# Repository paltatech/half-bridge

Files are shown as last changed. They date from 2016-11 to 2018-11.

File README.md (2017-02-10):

# TO247 Inverter power stage
This is the hardware repository of a 3 phase inverter, UNTESTED but designed with the following specs in mind:

* 70kw nominal, 150kw peak
* TO247 IGBT to allow for easy silicon upgrades and power capabilities. Its also cheaper.
* Watercooled
* Embedded security features (desaturation, soft turn off, reinforced isolation)


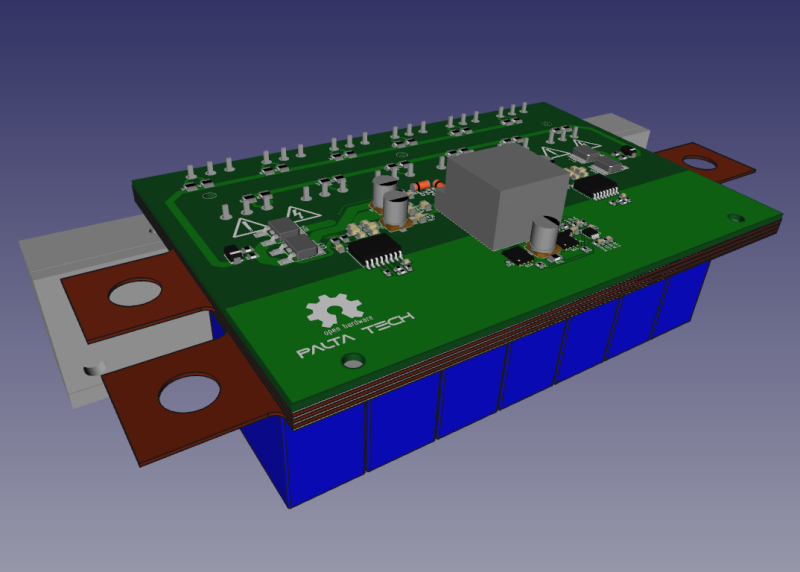
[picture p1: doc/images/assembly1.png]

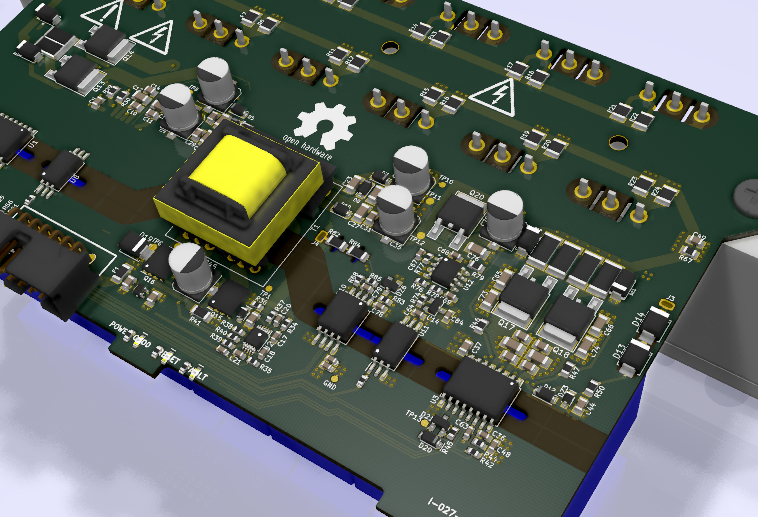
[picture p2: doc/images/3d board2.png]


You can also check the layout [here](https://eyrie.io/board?id=7261e811b9074e0fb00fe3fcbbaa14d9) 

Will need some cnc milling, components, a pcb, and some spot welding

Made open source with open source tools (kicad, freecad)

## Bill of materials
BOM, pcb gerbers, and custom parts can be found in [fabrication files](https://bitbucket.org/paltatech/half-bridge) directory

## License
This documentation describes Open Hardware and is licensed under the CERN OHL v. 1.2

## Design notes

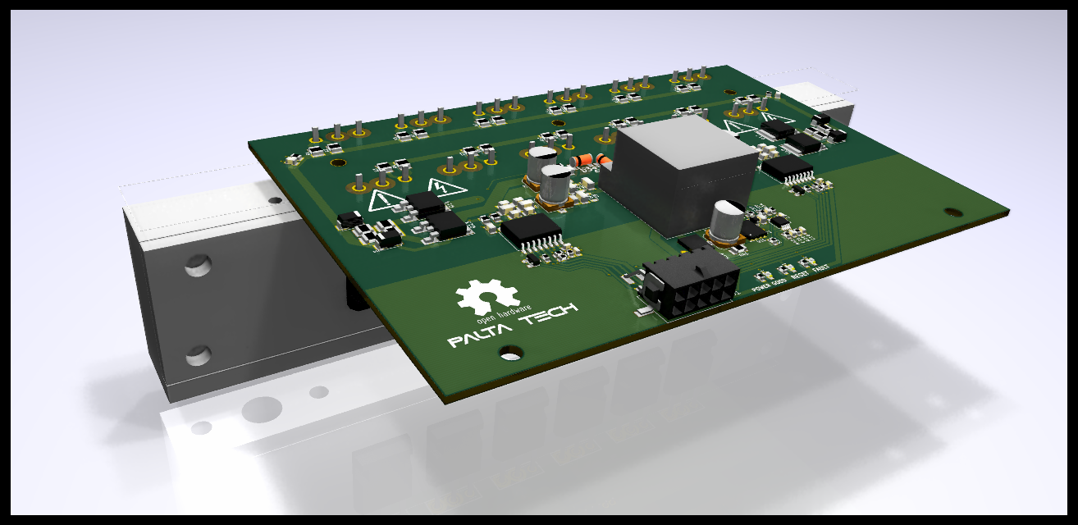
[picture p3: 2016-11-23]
doc/images/pcb_preview.png

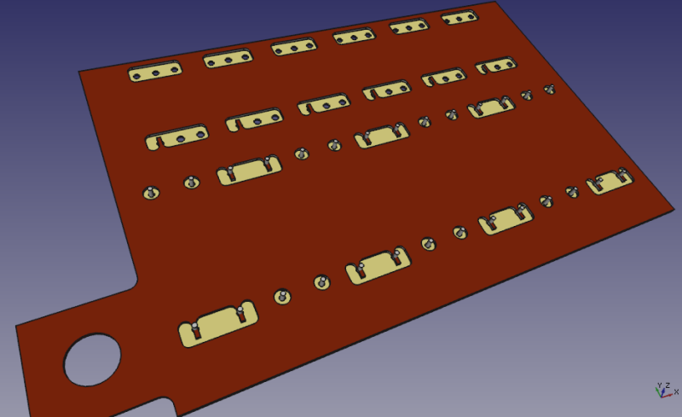
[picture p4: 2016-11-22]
doc/images/copper1.png

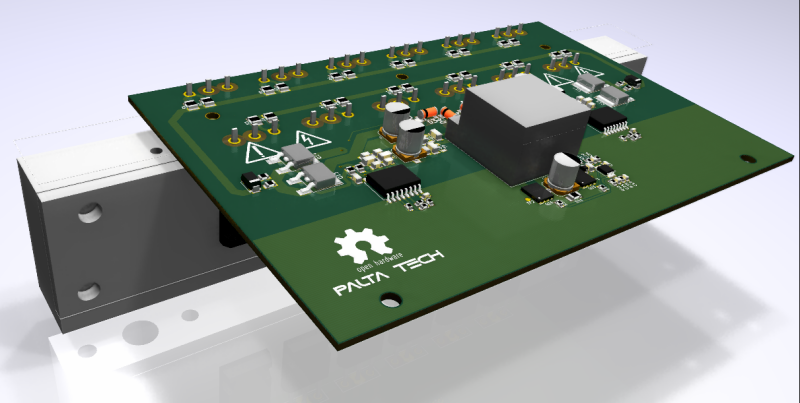
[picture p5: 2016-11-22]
doc/images/3d preview_2.png

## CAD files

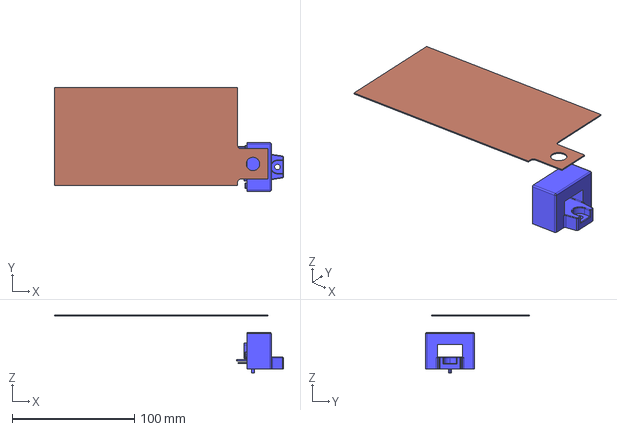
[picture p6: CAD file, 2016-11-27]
mechanical design/half bridge.fcstd
187.5 x 85.0 x 47.1 mm
PHASE
HASS_XXX-P

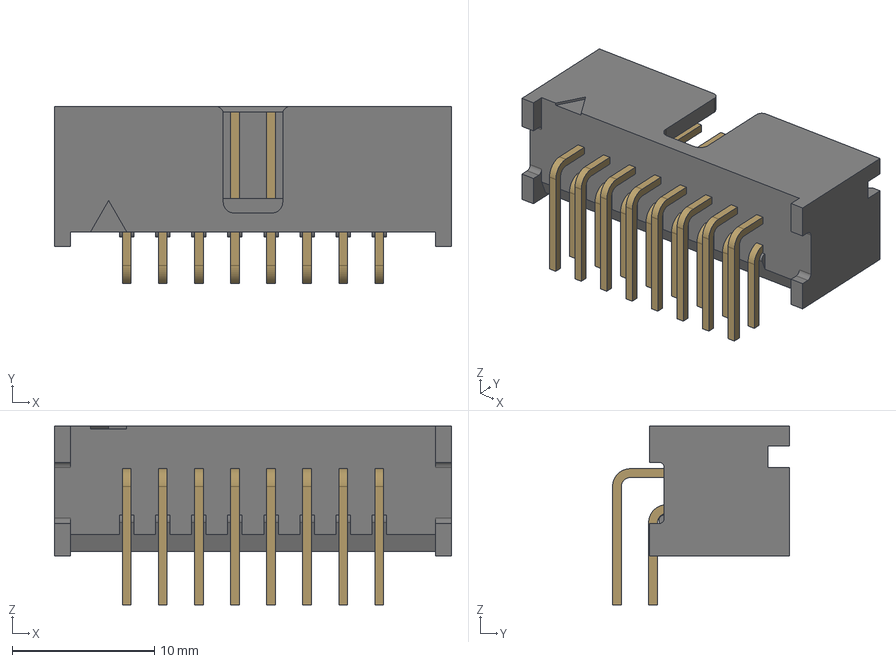
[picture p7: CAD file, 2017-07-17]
pcb design/3Dlib/c-5103310-3-b-3d.stp
27.9 x 12.5 x 12.6 mm

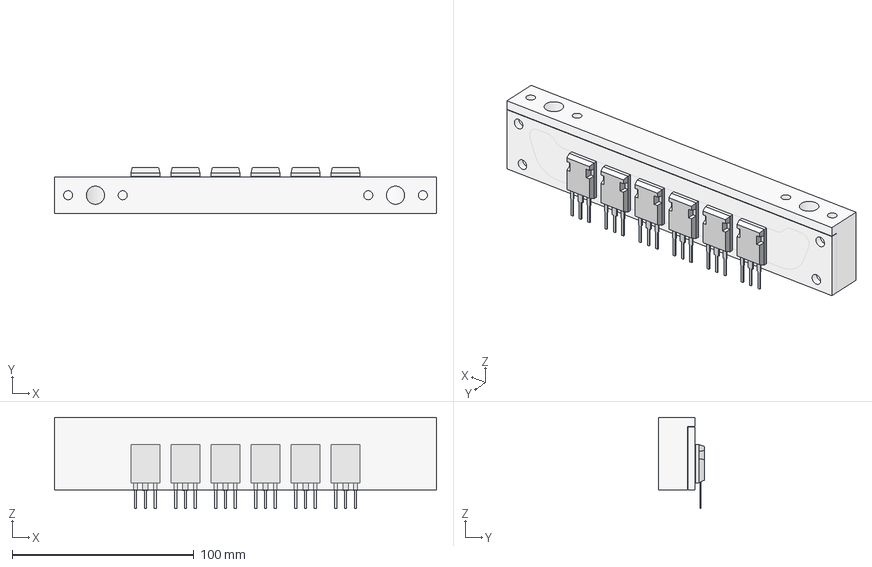
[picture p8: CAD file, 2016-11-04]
mechanical design/heatsink.fcstd
210.0 x 25.2 x 50.3 mm
heatsink-assembly

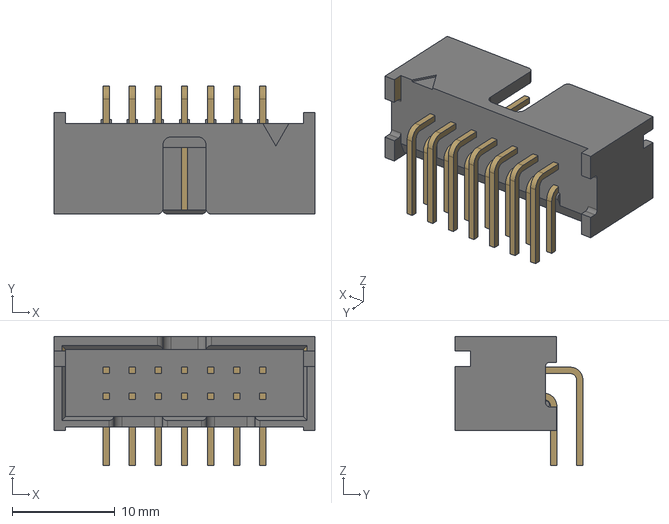
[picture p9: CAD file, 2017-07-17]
pcb design/3Dlib/c-5103310-2-b-3d.stp
25.4 x 12.5 x 12.6 mm

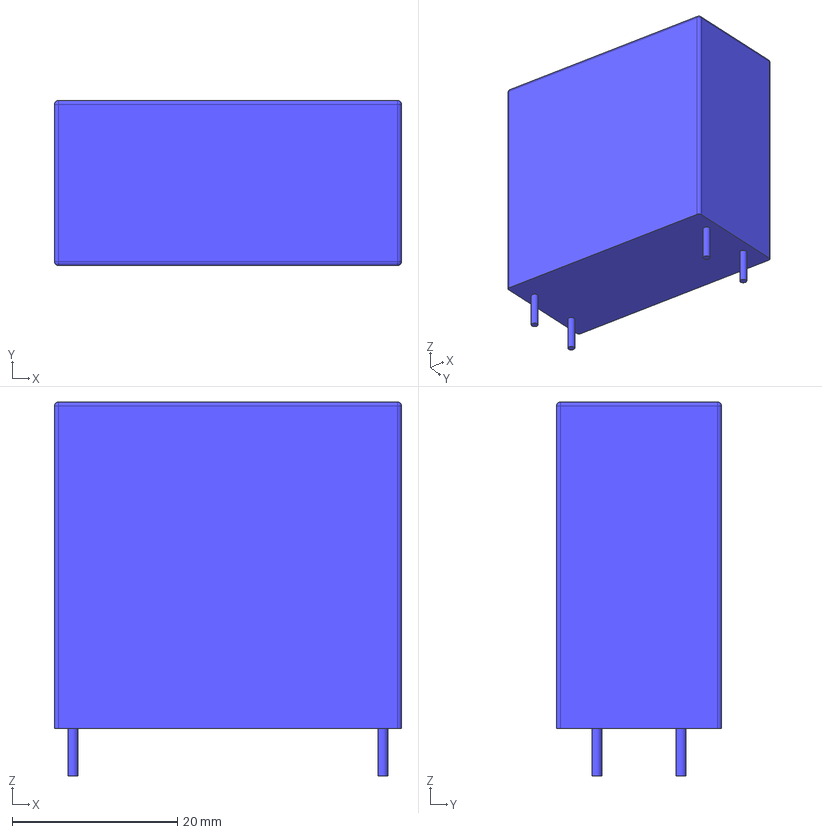
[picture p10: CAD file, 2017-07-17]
pcb design/3Dlib/EPCOS_film_cap.fcstd
42.0 x 20.0 x 45.2 mm

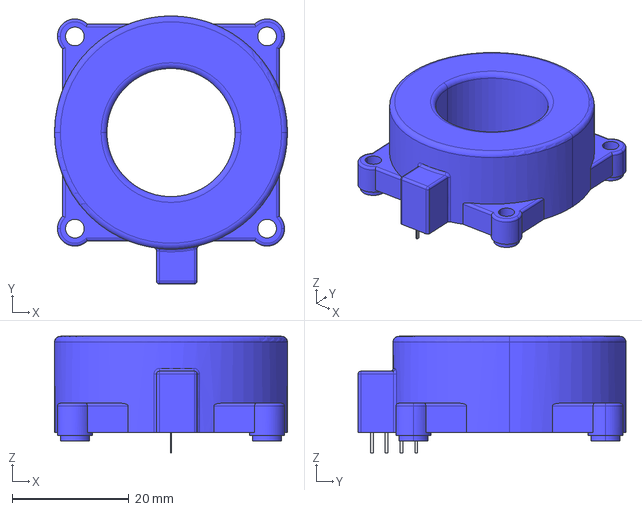
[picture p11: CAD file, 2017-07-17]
pcb design/3Dlib/HTFS_XXX-P.stp
40.0 x 46.0 x 20.0 mm

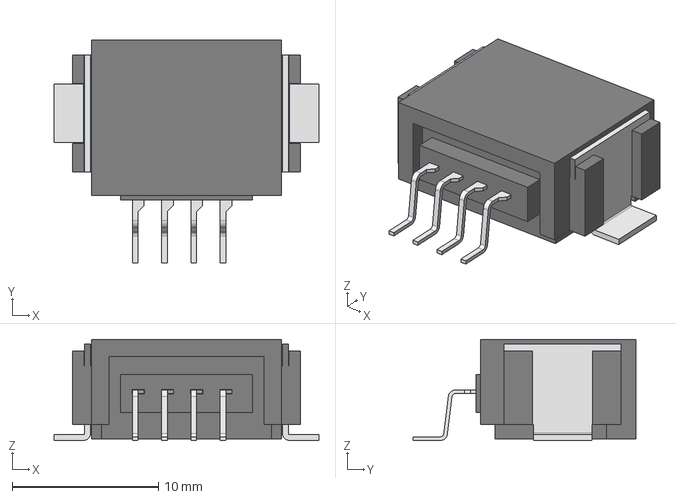
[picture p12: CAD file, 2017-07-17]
pcb design/3Dlib/SM04B1-CPTK-1A-TB.step
18.1 x 15.2 x 6.91 mm

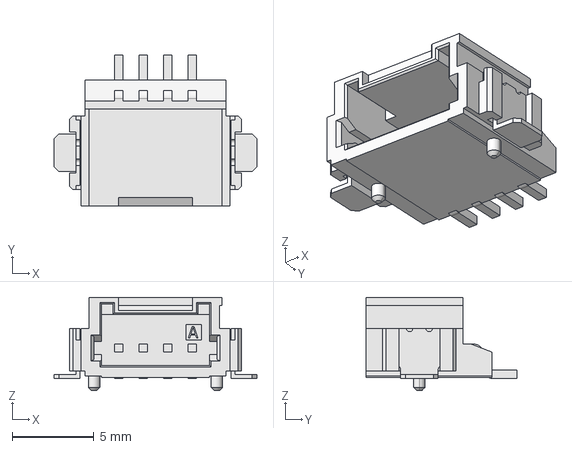
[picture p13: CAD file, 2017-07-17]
pcb design/3Dlib/c-0292227-04-a-3d.stp
12.4 x 9.20 x 5.70 mm

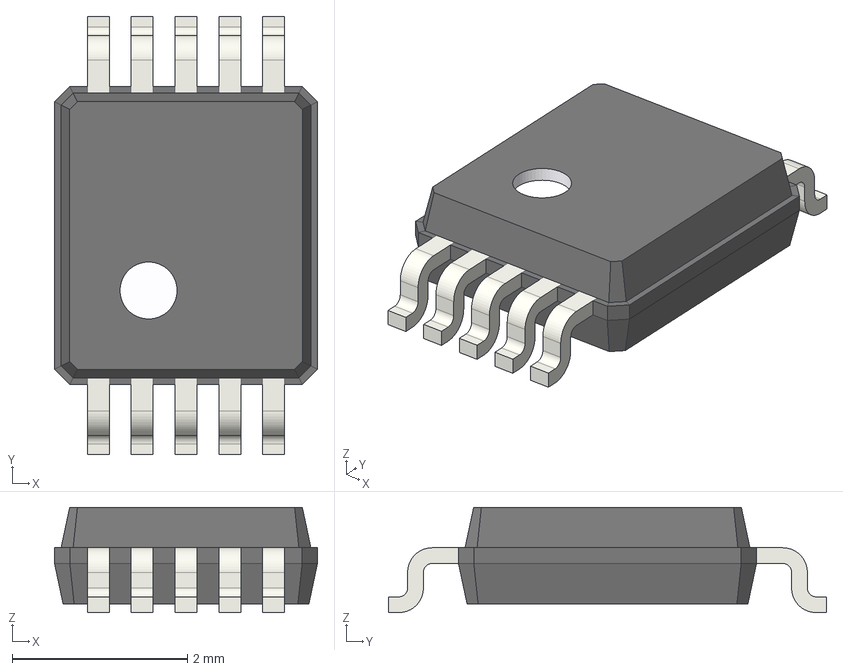
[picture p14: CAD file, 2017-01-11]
pcb design/3Dlib/tssop_10_30x30_p050.step
3.00 x 5.00 x 1.20 mm

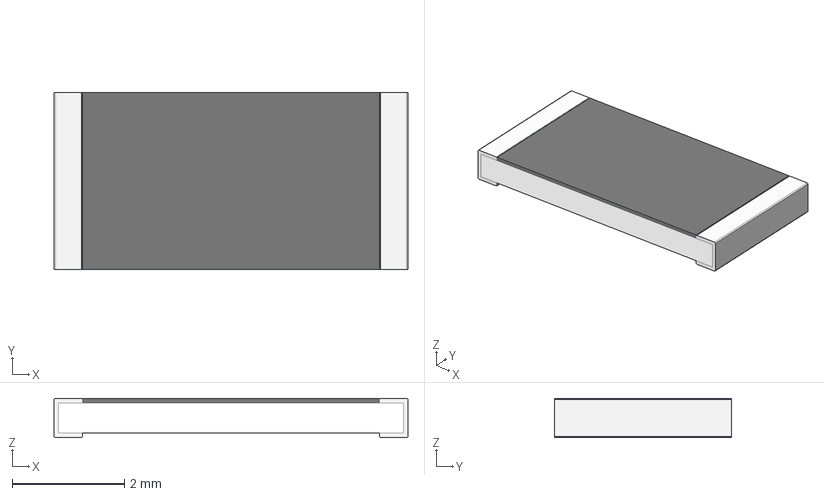
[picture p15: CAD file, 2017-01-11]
pcb design/3Dlib/r_2512_h070.step
6.30 x 3.15 x 0.7 mm

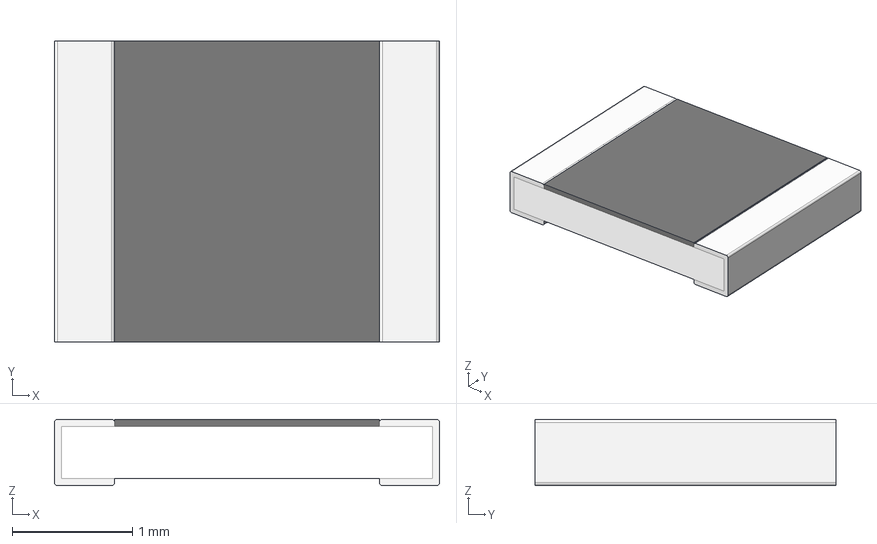
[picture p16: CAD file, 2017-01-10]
pcb design/3Dlib/r_1210_h055.step
3.20 x 2.50 x 0.55 mm

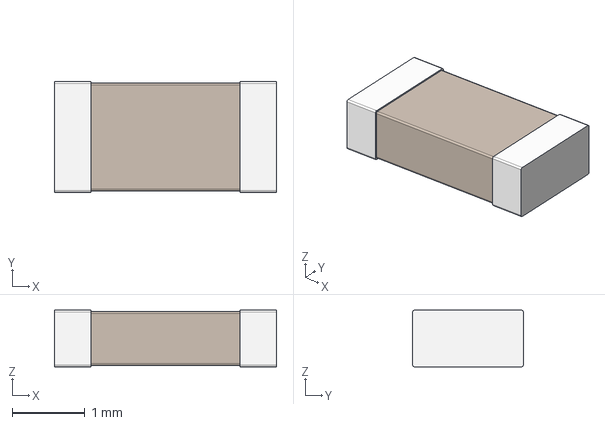
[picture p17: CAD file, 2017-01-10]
pcb design/3Dlib/c_1206_h078.step
3.05 x 1.52 x 0.78 mm

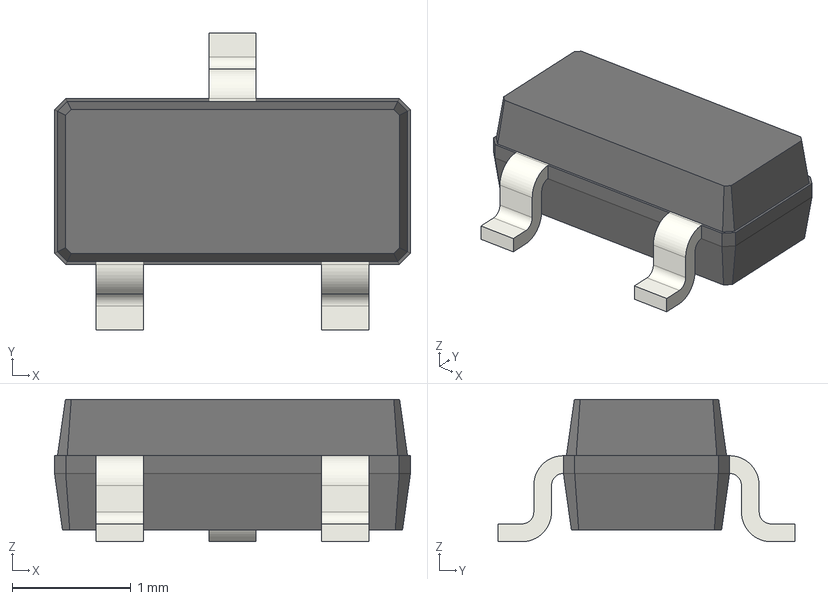
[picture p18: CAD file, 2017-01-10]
pcb design/3Dlib/sot23_3_25x30_p095.step
3.00 x 2.50 x 1.20 mm

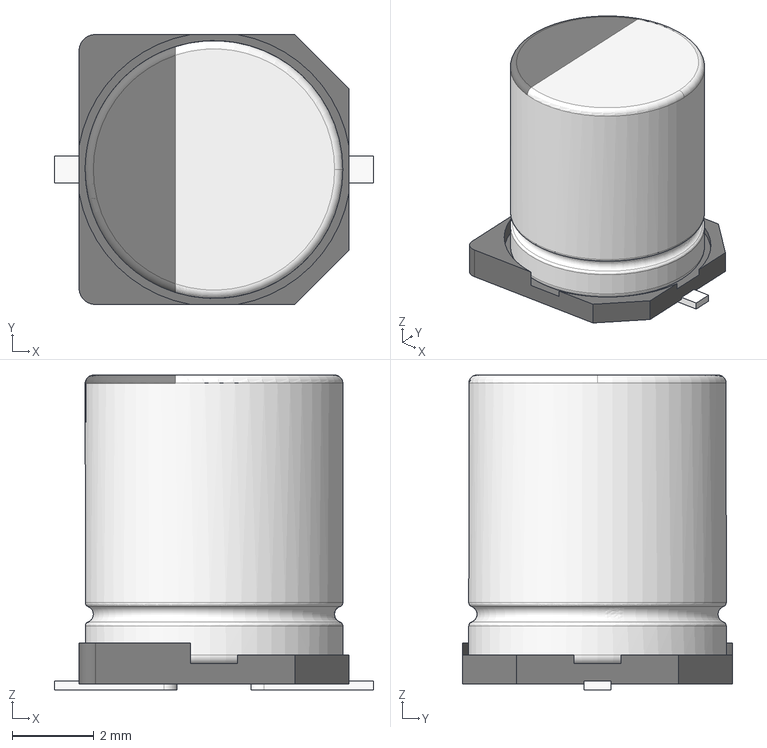
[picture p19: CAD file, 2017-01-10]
pcb design/3Dlib/c_el_D8_D63_L77.step
7.80 x 6.60 x 7.70 mm

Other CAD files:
pcb design/3Dlib/EPCOS_film_cap_B32796G3166.step
pcb design/3Dlib/r_0603_h078.step
pcb design/3Dlib/r_1206_h055.step
pcb design/3Dlib/soic_8_39x49_p127.step
pcb design/3Dlib/61001421121-rev1.step
pcb design/3Dlib/61031221121-rev1.stp
pcb design/3Dlib/750342312.fcstd
pcb design/3Dlib/BAS-M-R0002.step
pcb design/3Dlib/HASS_XXX-P.step
pcb design/3Dlib/HASS_XXX-P.stp
pcb design/3Dlib/M3_SMD_Standoff.fcstd
pcb design/3Dlib/M3_SMD_Standoff.step
pcb design/3Dlib/M3_SMD_Standoff_9mm.fcstd
pcb design/3Dlib/M3_SMD_Standoff_9mm.step
pcb design/3Dlib/M4 screw.fcstd
pcb design/3Dlib/M4_screw.step
pcb design/3Dlib/SOD-123.step
pcb design/3Dlib/TO-247-vertical.step
pcb design/3Dlib/c-4-794627-0-j-3d.step
pcb design/3Dlib/c-4-794627-0-j-3d.stp
pcb design/3Dlib/c_0603_h078.step
pcb design/3Dlib/c_0805_h078.step
pcb design/3Dlib/dpak-to252.step
pcb design/3Dlib/heatsink.step
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

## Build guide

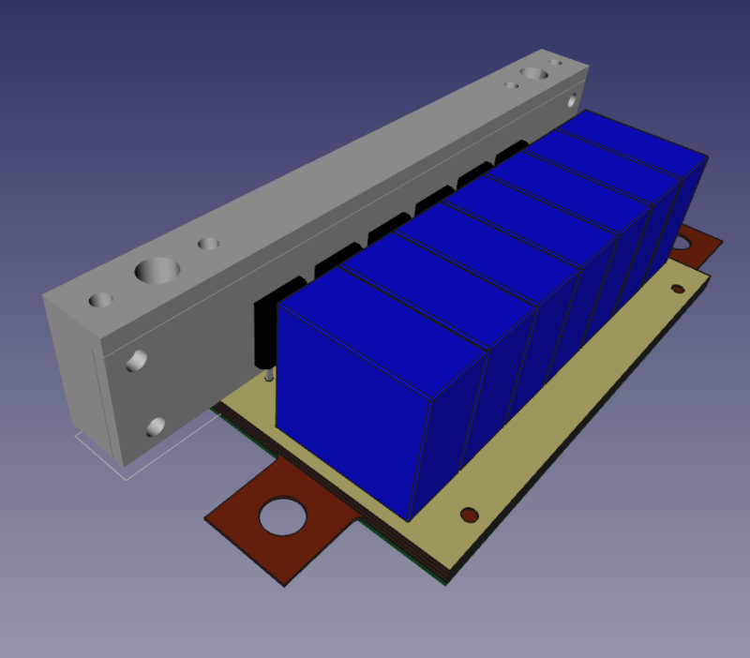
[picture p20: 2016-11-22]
doc/images/assembly2.png

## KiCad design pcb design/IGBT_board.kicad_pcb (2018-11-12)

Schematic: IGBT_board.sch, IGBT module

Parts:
C1, C2, C3, C4, C5, C6, C7: 16uF 700v; CAP_FILM_EPCOS_42x20mm_3D_only; mfg# B32796G3166K
C51, C52: 4.7uF; CAPC2012X70
C77, C82: 100pF; CAPC1608X55
C85: 1uF; CAPC1608X55
D19: TVS; Diode-SMB_Standard; mfg# SMBJ24A
DS1: FAULT; LED-0603
DS2: PWR_GOOD; LED-0603
DS3: RESET; LED-0603
F1: FUSE; RESC3216X60; mfg# 0ZCJ0050AF2E
J1: CONN-100MIL-M-2x8; MPN 5103310-3
J5: PHASE CURRENT CONN; TE-292227-4; MPN 292227-4
MP1: HEATSINK; heatsink-watercooled-20x210mm
Q1, Q2, Q3, Q4, Q5, Q6, Q7, Q8, Q9, Q10, Q11, Q12: IGBT; TO-247-HV; mfg# IXXX110N65B4H1
R1, R2: 1R; RESC3225X60
R3, R4, R5, R6, R7, R8, R9, R10, R11, R12, R13, R14, R15, R16, R17, R18, R19, R20, R21, R22, R23, R24: 20R; RESC3225X60; mfg# CRCW251220R0FKEG
R51, R52, R53: 1k; RESC1608X50
R54, R56, R59, R61: 22R; RESC1608X50
SYM1: OSHW-SCHEM-PCB10mm; Logo_silk_OSHW_12x13mm
U5: LM1117IMP-v.v; SOT-223

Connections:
+5: C52.1, C85.2, J5.1, R51.1, R52.1, R53.1, U5.2, U5.4; also elsewhere on the board
+24: C51.1, D19.1, F1.2, U5.3; also elsewhere on the board
/FAULT: DS1.1, R61.2; also elsewhere on the board
/I_phase+: J1.2, J5.2
/I_phase-: J1.1, J5.3
/PWM_N: C77.1, R54.2; also elsewhere on the board
/PWM_P: C82.2, R59.2; also elsewhere on the board
/PWR_GOOD: DS2.1; also elsewhere on the board
/RESET: DS3.1, R56.1; also elsewhere on the board
/SYNC: J1.8; also elsewhere on the board
/TEMP: J1.9
/VEE_CTRL: J1.7; also elsewhere on the board
/V_phase+: J1.4; also elsewhere on the board
/V_phase-: J1.3; also elsewhere on the board
GATE_HIGH: R1.1, R2.1, R5.1, R6.1, R9.1, R10.1, R13.1, R14.1, R17.1, R18.1, R21.1, R22.1; also elsewhere on the board
GATE_LOW: R3.1, R4.1, R7.1, R8.1, R11.1, R12.1, R15.1, R16.1, R19.1, R20.1, R23.1, R24.1; also elsewhere on the board
GND: C51.2, C52.2, C77.2, C82.1, C85.1, D19.2, J1.10, J1.14, J1.16, J5.4, U5.1; also elsewhere on the board
unnamed: DS1.2, R51.2
unnamed: DS2.2, R52.2
unnamed: DS3.2, R53.2
unnamed: F1.1, J1.13, J1.15
unnamed: J1.5, R56.2
unnamed: J1.6, R61.1
unnamed: J1.11, R59.1
unnamed: J1.12, R54.1
unnamed: Q1.1, R1.2, R2.2
unnamed: Q2.1, R3.2, R4.2
unnamed: Q3.1, R5.2, R6.2
unnamed: Q4.1, R7.2, R8.2
unnamed: Q5.1, R9.2, R10.2
unnamed: Q6.1, R11.2, R12.2
unnamed: Q7.1, R13.2, R14.2
unnamed: Q8.1, R15.2, R16.2
unnamed: Q9.1, R17.2, R18.2
unnamed: Q10.1, R19.2, R20.2
unnamed: Q11.1, R21.2, R22.2
unnamed: Q12.1, R23.2, R24.2
PHASE: Q1.3, Q2.2, Q3.3, Q4.2, Q5.3, Q6.2, Q7.3, Q8.2, Q9.3, Q10.2, Q11.3, Q12.2; also elsewhere on the board
VBUS+: Q1.2, Q3.2, Q5.2, Q7.2, Q9.2, Q11.2; also elsewhere on the board
VBUS-: Q2.3, Q4.3, Q6.3, Q8.3, Q10.3, Q12.3; also elsewhere on the board

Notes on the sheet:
Highest performance IGBT I found: AUIRGPS4067D1 reasonable performance: IXXX110N65B4H1 tesla used IKW75N60TFKSA1
The plan is to design it for 70kw continuous, 200kw peak So, at 400v you need 175 Amp per phase (70kw current x 2.5). That is 30A per IGBT At 30A, 0.9v Vce = 27W per transistor aim to 50-50 power losses (switching and sat) At 45°C ambient temperature, if we want 75°C Junction temp, its a 30°C dT, a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
Sil-pad thermal: SPK4-0.006-00-11.512 kapton? hard anodized aluminum? gel immersion? (could help with igbt-heatsink cleareances)
Capacitors must be able to supply roughly 65% of battery supplied current, so its important to have enough rms current in the cap bank. In this case, if we plan for 200kW at 500A, we should expect a total RMS current of 325A in the capacitors. We have 16uF*7*3 = 336uF 14Arms per cap -> 98Arms per m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
For BOM creator: kicad_bom_wizard "%I" "%O.csv" "CSV"
(FILM)
PHASE LEG IGBT MODULE
deadtime calculation: * input filter * igbt driver: 30ns(skew)+25ns(rise/fall delta) + * boost transistor: * IGBT:
Rg < Rgdriver / N / 10 for lower Rg mismatch
Use common mode chokes?

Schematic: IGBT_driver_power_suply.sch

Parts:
C17: 1uF; CAPC1608X55
C18: 22nF; CAPC1608X55
C19: 22uF 16v; CAPC2012X70
C20: 1nF; CAPC1608X55
C21: 470pF; CAPC1608X55
C22, C23, C24, C25, C26, C27, C53, C54: 10uF 50v; CAPC3216X70; mfg# CL31A106KBHNNNE
C28, C29, C30, C31: 100nF 50v; CAPC2012X70; mfg# 08055C104JAT2A
C32, C33, C34, C35, C45: 47uF 50v; c_elec_6.3x7.7; mfg# EEE-FK1H470XP
C50: 100pF; CAPC1608X55
D5, D6, D7, D8, D9, D10, D22, D23: RB160MM-60TR; SOD-123F; mfg# RB160MM-60TR
DZ2: MM3Z12VB; SOD-323F; mfg# MM3Z12VB
Q15, Q16: CSD19533Q5A; TEXAS-Q5A; mfg# CSD19533Q5A
R34, R37: 0R; RESC1608X50
R35: 26.7k; RESC1608X50
R36, R40: 1.15k; RESC1608X50
R38, R39: 22R; RESC1608X50
R41: 0.22R; RESC3216X60
T1: TRANS-3-1CT; wurth_750342312; mfg# 750342312
TP1: SW1; TEST-SMD-SMALL
TP2: SW2; TEST-SMD-SMALL
TP6: 24v; TEST-SMD-SMALL
TP7, TP10: 15v; TEST-SMD-SMALL
TP8, TP11: GND; TEST-SMD-SMALL
TP9, TP12: -15v; TEST-SMD-SMALL
U2: LM5030; TSSOP-10_3x3mm_Pitch0.5mm; mfg# LM5030MM/NOPB

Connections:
+24: C45.1, R34.2, R36.1, T1.3, TP6.1; also elsewhere on the board
/IGBT_driver_BOT/+15V: C26.1, C30.1, C34.1, D7.1, TP10.1; also elsewhere on the board
/IGBT_driver_BOT/-15V: C27.2, C31.2, C35.2, D23.2, TP12.1; also elsewhere on the board
/IGBT_driver_TOP/+15V: C24.1, C28.1, C32.1, D5.1, TP7.1; also elsewhere on the board
/IGBT_driver_TOP/-15V: C25.2, C29.2, C33.2, D22.2, TP9.1; also elsewhere on the board
/SYNC: C50.1; also elsewhere on the board
/isolated power supply/CS: C21.1, R40.2, U2.8
GND: C17.1, C18.1, C19.2, C20.2, C21.2, C45.2, DZ2.2, R35.2, R41.2, U2.2, U2.7; also elsewhere on the board
unnamed: C17.2, R34.1, U2.1
unnamed: C18.2, U2.10
unnamed: C19.1, DZ2.1, R36.2, U2.4
unnamed: C20.1, R37.2
unnamed: C22.1, D5.2, D6.1
unnamed: C22.2, C53.2, T1.13
unnamed: C23.1, D7.2, D8.1
unnamed: C23.2, C54.2, T1.8
unnamed: C50.2, R35.1, U2.9
unnamed: C53.1, D9.2, D22.1
unnamed: C54.1, D10.2, D23.1
unnamed: Q15.1, Q15.2, Q15.3, Q16.1, Q16.2, Q16.3, R40.1, R41.1
unnamed: Q15.4, R38.1
unnamed: Q15.5, Q15.6, Q15.7, Q15.8, T1.5, TP1.1
unnamed: Q16.4, R39.2
unnamed: Q16.5, Q16.6, Q16.7, Q16.8, T1.1, TP2.1
unnamed: R37.1, U2.3
unnamed: R38.2, U2.5
unnamed: R39.1, U2.6
PHASE: C24.2, C25.1, C28.2, C29.1, C32.2, C33.1, D6.2, D9.1, T1.14, TP8.1; also elsewhere on the board
VBUS-: C26.2, C27.1, C30.2, C31.1, C34.2, C35.1, D8.2, D10.1, T1.7, TP11.1; also elsewhere on the board

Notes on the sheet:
Power calculation according to http://www.ti.com/lit/ug/tidu355a/tidu355a.pdf 0.6W+(0.000000183C*6)*20000Hz*(15v+8v)+(0.000000005500F*6)*20000Hz*(15v+8v)^2 = 1.45 W
Left side corresponds to http://www.ti.com/lit/ug/tidu355a/tidu355a.pdf Right side corresponds to TIDUA15A
Dual Isolated +15v -15v power supply 2W per IGBT bank
check MGJ2D241509SC
Controlling pwm from MCU could help with harmonics, or maybe sync it with the leg switching freq
Always check the actual capacitance you get at the operating voltage. These curves are for samsung's MLCC caps
weird way to draw a transformer... fix it
About syncing: * External source frequency must be higher than configured frequency (configured with RT) * 15nsec to 150nsec pulse width * 1.5V to 3.0V signal amplitude Why syncing? Phase voltage sampling could be measured at the same point in the power supply ripple. You can avoid switching the su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
Frequency setting with RT. R = (1/F - 172E-9) / 182e-12 So, eval board was switching at 200khz. Figure out why, this transformer is supposed to be operated at 500khz
10k ohm would set this to 500KHz...
For +15/-8v operation, short C53/C54 and remove D9/D10
Ensure <30pF transformer capacitance Less in case of SiC drives.where 5pF will inject 250mA at 50V/ns (dV/dt) in the control side. Adding mounting point for grounding these switching currents to the chassis so they don't travel across control wiring.

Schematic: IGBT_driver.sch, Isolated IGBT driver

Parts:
C8, C83: 100nF; CAPC1608X55
C9, C10, C11: 1uF 50v; CAPC2012X70; mfg# CL21B105KBFNNNE
C12, C13, C57, C58, C71, C72: 10uF 50v; CAPC3216X70; mfg# CL31A106KBHNNNE
C14, C15: 100nF 50v; CAPC2012X70; mfg# 08055C104JAT2A
C16: 100pF COG; CAPC2012X70; mfg# C0805C101J5GACTU
C46: 10uF; CAPC1608X55
C47: 5nF 50v; CAPC2012X70
C55: 1nF; CAPC1608X55
C56: 1uF; CAPC1608X55
C87: 10nF; CAPC1608X55
D1, D16: SK310A-LTP; do214ac; mfg# SK310A-LTP
D2: RB168MM-60TR; SOD-123F; mfg# RB168MM-60TR
D3, D4: MURS160-13-F; Diode-SMB_Standard; mfg# MURS160-13-F
D15: 1N4148W; SOD-123
D17: GSOT03C; SOT-23; mfg# GSOT03C-E3-08
D25: ES2J-LTP; DIOM5226X203; MPN ES2J-LTP
DZ1: MM3Z12VB; SOD-323F; mfg# MM3Z12VB
DZ5: SMCJ440CA; DIOM7959X265; MPN SMCJ440CA
J2: DESAT; CONN-100MIL-F-1x1
Q13: NPN; DPAK-2; mfg# MJD3055T4G
Q14: PNP; DPAK-2; mfg# MJD2955T4G
R25, R26: 10k; RESC1608X50
R27: 10R; RESC1608X50
R28: 4.7k; RESC1608X50
R29, R30: 12R; RESC2012X50
R31, R32: 3R; RESC6432X70; mfg# PCNM2512K3R00FST5
R33: 1k; RESC2012X50
R58: 1k; RESC1608X50
R60: 4.7k; RESC2012X50
R62: 12R; RESC1608X50; mfg# RC0603FR-07390RL
R68, R93: 390R; RESC1608X50; mfg# RC0603FR-07390RL
R69: NI; RESC6432X70
R75: NI; RESC6432X70; MPN PCNM1206K2R00FST5
TP3: IN; TEST-SMD-SMALL
TP4: GND; TEST-SMD-SMALL
U1: ISO5852S; SOIC-16_7.5x10.3mm_Pitch1.27mm; mfg# ISO5852SQDWRQ1
U8: SI8710B; SDIP6; mfg# SI8710BD-B-IS
U13: LM3480; SOT-23; mfg# LM3480IM3X-12/NOPB

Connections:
+5: C46.1, R25.1, R26.1, R27.1; also elsewhere on the board
/FAULT: D15.1, R25.2, U1.13; also elsewhere on the board
/IGBT_driver_TOP/12.0V: C56.1, R68.2, U8.6 (VCC), U13.1 (OUT)
/IGBT_driver_TOP/+15V: C10.1, C12.1, C14.1, C57.1, C71.1, C83.1, D16.1, Q13.2, U1.5, U13.2 (IN); also elsewhere on the board
/IGBT_driver_TOP/-VEE: C9.2, C11.2, C13.2, C15.2, C58.2, C72.2, C87.2, D1.2, Q14.2, U1.1, U1.8; also elsewhere on the board
/IGBT_driver_TOP/supply control/PWM: R68.1, U8.5 (Vo); also elsewhere on the board
/PWM_N: D17.2, R28.1, U1.11; also elsewhere on the board
/PWM_P: D15.2, D17.1, R58.1, TP3.1, U1.10; also elsewhere on the board
/PWR_GOOD: R26.2, U1.12; also elsewhere on the board
/RESET: C55.1, U1.14; also elsewhere on the board
/VEE_CTRL: R93.2; also elsewhere on the board
GATE_HIGH: C47.1, D1.1, D16.2, D25.1, R31.1, R32.1, R60.2, R69.1, R75.1; also elsewhere on the board
GND: C8.2, C46.2, C55.2, D17.3, R28.2, R58.2, TP4.1, U1.9, U1.16, U8.3 (K); also elsewhere on the board
unnamed: C8.1, R27.2, U1.15
unnamed: C16.1, D2.1, DZ1.1, R33.2, U1.2
unnamed: C87.1, R62.1
unnamed: D3.1, D4.2
unnamed: D3.2, R33.1
unnamed: D25.2, DZ5.2
unnamed: Q13.1, Q14.1, R29.1, R30.1
unnamed: Q13.3, R31.2, R69.2
unnamed: Q14.3, R32.2, R75.2
unnamed: R29.2, U1.4
unnamed: R30.2, R62.2, U1.6
unnamed: R93.1, U8.1 (A)
PHASE: C9.1, C10.2, C11.1, C12.2, C13.1, C14.2, C15.1, C16.2, C47.2, C56.2, C57.2, C58.1, C71.2, C72.1, C83.2, D2.2, DZ1.2, R60.1, U1.3, U8.4 (GND), U13.3; also elsewhere on the board
VBUS+: D4.1, DZ5.1, J2.1; also elsewhere on the board

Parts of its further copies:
C36, C84: 100nF; CAPC1608X55
C37, C38, C39: 1uF 50v; CAPC2012X70; mfg# CL21B105KBFNNNE
C40, C41, C65, C66, C73, C74: 10uF 50v; CAPC3216X70; mfg# CL31A106KBHNNNE
C42, C43: 100nF 50v; CAPC2012X70; mfg# 08055C104JAT2A
C44: 100pF COG; CAPC2012X70; mfg# C0805C101J5GACTU
C48: 10uF; CAPC1608X55
C49: 5nF 50v; CAPC2012X70
C63: 1nF; CAPC1608X55
C64: 1uF; CAPC1608X55
C86: 10nF; CAPC1608X55
D11, D18: SK310A-LTP; do214ac; mfg# SK310A-LTP
D12: RB168MM-60TR; SOD-123F; mfg# RB168MM-60TR
D13, D14: MURS160-13-F; Diode-SMB_Standard; mfg# MURS160-13-F
D20: 1N4148W; SOD-123
D21: GSOT03C; SOT-23; mfg# GSOT03C-E3-08
D24: ES2J-LTP; DIOM5226X203; MPN ES2J-LTP
DZ3: MM3Z12VB; SOD-323F; mfg# MM3Z12VB
DZ4: SMCJ440CA; DIOM7959X265; MPN SMCJ440CA
J3: DESAT; CONN-100MIL-F-1x1
Q17: NPN; DPAK-2; mfg# MJD3055T4G
Q18: PNP; DPAK-2; mfg# MJD2955T4G
R42, R43: 10k; RESC1608X50
R44: 10R; RESC1608X50
R45: 4.7k; RESC1608X50
R46, R47: 12R; RESC2012X50
R48, R49: 3R; RESC6432X70; mfg# PCNM2512K3R00FST5
R50: 1k; RESC2012X50
R55: 12R; RESC1608X50; mfg# RC0603FR-07390RL
R57: 1k; RESC1608X50
R67: 4.7k; RESC2012X50
R74, R94: 390R; RESC1608X50; mfg# RC0603FR-07390RL
R89: NI; RESC6432X70
R90: NI; RESC6432X70; MPN PCNM1206K2R00FST5
TP13: IN; TEST-SMD-SMALL
TP14: GND; TEST-SMD-SMALL
U3: ISO5852S; SOIC-16_7.5x10.3mm_Pitch1.27mm; mfg# ISO5852SQDWRQ1
U11: SI8710B; SDIP6; mfg# SI8710BD-B-IS
U14: LM3480; SOT-23; mfg# LM3480IM3X-12/NOPB

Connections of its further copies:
+5: C48.1, R42.1, R43.1, R44.1; also elsewhere on the board
/FAULT: D20.1, R42.2, U3.13; also elsewhere on the board
/IGBT_driver_BOT/12.0V: C64.1, R74.2, U11.6 (VCC), U14.1 (OUT)
/IGBT_driver_BOT/+15V: C38.1, C40.1, C42.1, C65.1, C73.1, C84.1, D18.1, Q17.2, U3.5, U14.2 (IN); also elsewhere on the board
/IGBT_driver_BOT/-VEE: C37.2, C39.2, C41.2, C43.2, C66.2, C74.2, C86.2, D11.2, Q18.2, U3.1, U3.8; also elsewhere on the board
/IGBT_driver_BOT/supply control/PWM: R74.1, U11.5 (Vo); also elsewhere on the board
/PWM_N: D20.2, D21.1, R57.1, TP13.1, U3.10; also elsewhere on the board
/PWM_P: D21.2, R45.1, U3.11; also elsewhere on the board
/PWR_GOOD: R43.2, U3.12; also elsewhere on the board
/RESET: C63.1, U3.14; also elsewhere on the board
/VEE_CTRL: R94.2; also elsewhere on the board
GATE_LOW: C49.1, D11.1, D18.2, D24.1, R48.1, R49.1, R67.2, R89.1, R90.1; also elsewhere on the board
GND: C36.2, C48.2, C63.2, D21.3, R45.2, R57.2, TP14.1, U3.9, U3.16, U11.3 (K); also elsewhere on the board
unnamed: C36.1, R44.2, U3.15
unnamed: C44.1, D12.1, DZ3.1, R50.2, U3.2
unnamed: C86.1, R55.1
unnamed: D13.1, D14.2
unnamed: D13.2, R50.1
unnamed: D24.2, DZ4.2
unnamed: Q17.1, Q18.1, R46.1, R47.1
unnamed: Q17.3, R48.2, R89.2
unnamed: Q18.3, R49.2, R90.2
unnamed: R46.2, U3.4
unnamed: R47.2, R55.2, U3.6
unnamed: R94.1, U11.1 (A)
PHASE: D14.1, DZ4.1, J3.1; also elsewhere on the board
VBUS-: C37.1, C38.2, C39.1, C40.2, C41.1, C42.2, C43.1, C44.2, C49.2, C64.2, C65.2, C66.1, C73.2, C74.1, C84.2, D12.2, DZ3.2, R67.1, U3.3, U11.4 (GND), U14.3; also elsewhere on the board

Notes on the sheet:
ISO5852S isolated gate driver with current buffering
5kV RMS Isolation barrier
Gate resistor power rating: Check www.goo.gl/HwrKMw Its around 2.5W ON (and we have up to 8W) and 0.6W OFF (and we have up to 8W). (8W in an ideal pcb layout that we won't have) Try to find something like this http://www.isabellenhuette.de/fileadmin/content/praezisions-leistungswiderstaende/SMP.PDF
TH to connect to copper collector layer
drive a 100 khz PWM
Keep decoupling caps close to the transistors
non-magnetic, pulse withstanding resistors!
When FAULT is asserted externally, mute the input
(blanking cap) With this cap you tune the desat response time. SiC mosfets need to enter soft turn off in less than 3us. IGBTs have larger parasitic capacitance so its not possible to use such short times. IGBTs can withstand almost 10us.
10 Ohm vishay resistors come in 0.1% 25ppm for the same price of 1% 100ppm 2 ohm
(50ns recovery time)
Latchup protection. A latchup here blows IGBTs
12V 200mW zener for protection
Ensures IGBT is OFF while driver is powered off
input protection. You don't want a latch-up here
High wattage, and hard to heatsink
20uA leakage at 125°C
Needed for soft turn-off when current boost is used (tiduc70a 2.1.7)
Active overvoltage clamping for high fault current turn-off
AEC Q-101: MJD44H11 and MJD45H11

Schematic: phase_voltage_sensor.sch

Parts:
C78, C80: 100nF; CAPC1608X55
C79: 330pF; CAPC1608X55
C81: 2.2uF; CAPC1608X55
DZ6: 5v; SOT-23; MPN BZX84-A5V1,215
J4: PHASE; CONN-100MIL-F-1x1
R82, R84: 1M; RESC3216X60; MPN CHV1206-FX-1004ELF
R83: 12R; RESC1608X50
R85, R88: 1k; RESC1608X50
U10: AMC1301; SOIC127P1032X265-8; MPN AMC1301DWVR

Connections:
+5: C80.1, C81.1, U10.8 (VDD2); also elsewhere on the board
/IGBT_driver_BOT/+15V: R83.2; also elsewhere on the board
/V_phase+: U10.7 (VOUTP); also elsewhere on the board
/V_phase-: U10.6 (VOUTN); also elsewhere on the board
/phase voltage/VIN+: C79.1, R84.1, R85.1, U10.2 (VINP)
/phase voltage/VIN-: C79.2, R88.2, U10.3 (VINN)
GND: C80.2, C81.2, U10.5 (GND2); also elsewhere on the board
unnamed: C78.2, DZ6.3, R83.1, U10.1 (VDD1)
unnamed: R82.1, R84.2
PHASE: J4.1, R82.2; also elsewhere on the board
VBUS-: C78.1, DZ6.1, R85.2, R88.1, U10.4 (GND1); also elsewhere on the board

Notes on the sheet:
=1000/(2000000+2000)*650*8.2 = 2.66V differential output at 650V
These particular 1206 resistors are rated at 800V each. Put slots though
0-650V phase voltage measurement using isolation amplifier
Route very close together

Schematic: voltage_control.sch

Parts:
C67, C69: 10nF; CAPC1608X55
C68: 100nF; CAPC1608X55
C70: 47uF 50v; c_elec_6.3x7.7; mfg# EEE-FK1H470XP
C75: 10uF 50v; CAPC3216X70; mfg# CL31A106KBHNNNE
Q19: PNP; DPAK-2; mfg# MJD2955T4G
R73: 100R; RESC2012X50
R76, R77, R78: 10k; RESC1608X50
U12: OPA2172; SOIC127P600X175-8; MPN OPA2172IDR

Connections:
/IGBT_driver_BOT/+15V: C68.2, U12.8; also elsewhere on the board
/IGBT_driver_BOT/-15V: C68.1, U12.4; also elsewhere on the board
/IGBT_driver_BOT/-VEE: C70.2, U12.6; also elsewhere on the board
/IGBT_driver_BOT/supply control/PWM: R76.2; also elsewhere on the board
/IGBT_driver_TOP/-15V: Q19.2; also elsewhere on the board
/IGBT_driver_TOP/-VEE: C75.1, Q19.3; also elsewhere on the board
unnamed: C67.1, R76.1, R77.2, U12.2
unnamed: C67.2, R77.1, R78.2, U12.1
unnamed: C69.2, R78.1, U12.5
unnamed: Q19.1, R73.1
unnamed 100: R73.2; also elsewhere on the board
unnamed 101: U12.7; also elsewhere on the board
PHASE: C75.2; also elsewhere on the board
VBUS-: C69.1, C70.1, U12.3; also elsewhere on the board

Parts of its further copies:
C59, C61: 10nF; CAPC1608X55
C60: 100nF; CAPC1608X55
C62: 47uF 50v; c_elec_6.3x7.7; mfg# EEE-FK1H470XP
C76: 10uF 50v; CAPC3216X70; mfg# CL31A106KBHNNNE
Q20: PNP; DPAK-2; mfg# MJD2955T4G
R70, R71, R72: 10k; RESC1608X50
R79: 100R; RESC2012X50
U9: OPA2172; SOIC127P600X175-8; MPN OPA2172IDR

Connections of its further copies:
/IGBT_driver_BOT/-15V: Q20.2; also elsewhere on the board
/IGBT_driver_BOT/-VEE: C76.1, Q20.3; also elsewhere on the board
/IGBT_driver_TOP/+15V: C60.2, U9.8; also elsewhere on the board
/IGBT_driver_TOP/-15V: C60.1, U9.4; also elsewhere on the board
/IGBT_driver_TOP/-VEE: C62.2, U9.6; also elsewhere on the board
/IGBT_driver_TOP/supply control/PWM: R70.2; also elsewhere on the board
unnamed: C59.1, R70.1, R71.2, U9.2
unnamed: C59.2, R71.1, R72.2, U9.1
unnamed: C61.2, R72.1, U9.5
unnamed: Q20.1, R79.1
unnamed 100: U9.7; also elsewhere on the board
unnamed 101: R79.2; also elsewhere on the board
PHASE: C61.1, C62.1, U9.3; also elsewhere on the board
VBUS-: C76.2; also elsewhere on the board

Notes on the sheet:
+-75mA output
Simulation: step response (0->90%) in 0.4msec 100kHz PWM
Negative power supply programmable with PWM
0% duty -> -1V 100% duty -> - 9V
Try to heatsink this pnp
AD8397 drives more current

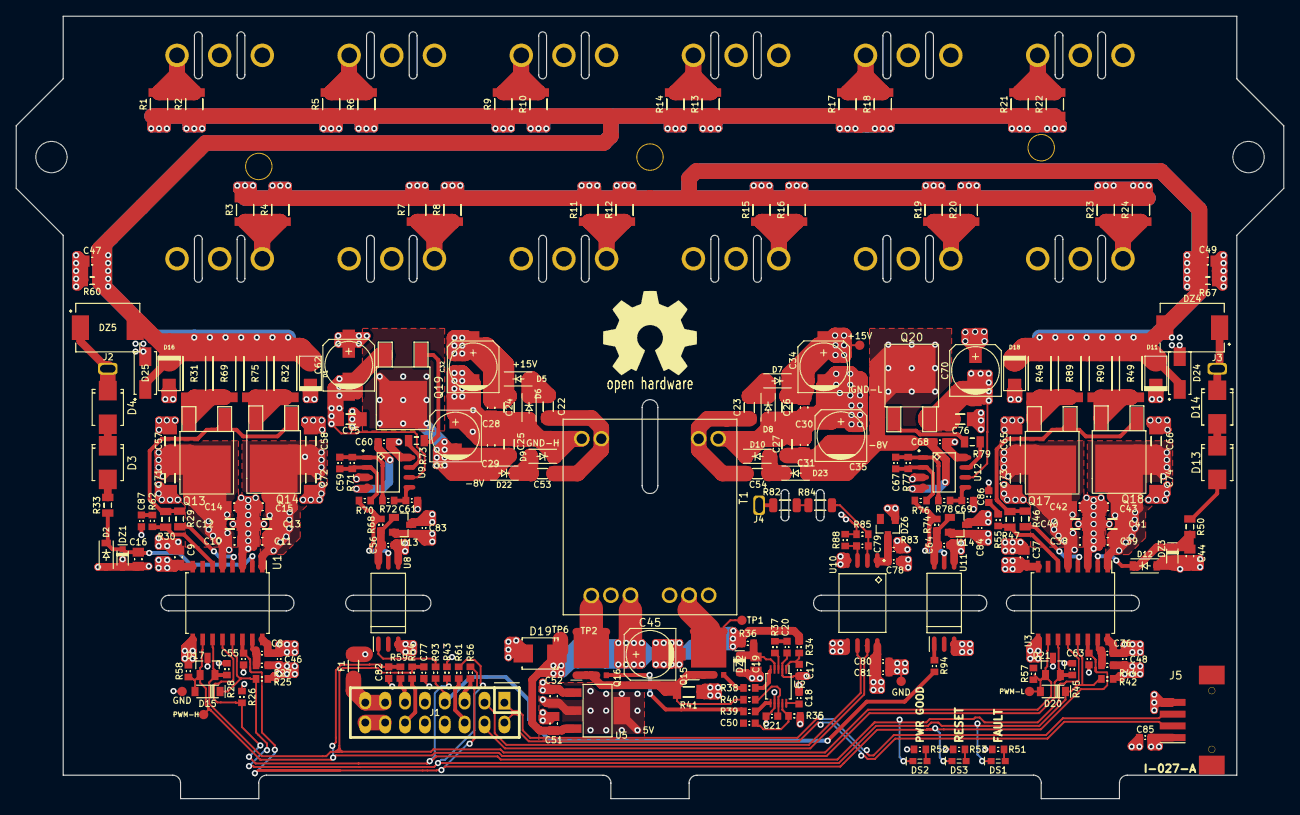
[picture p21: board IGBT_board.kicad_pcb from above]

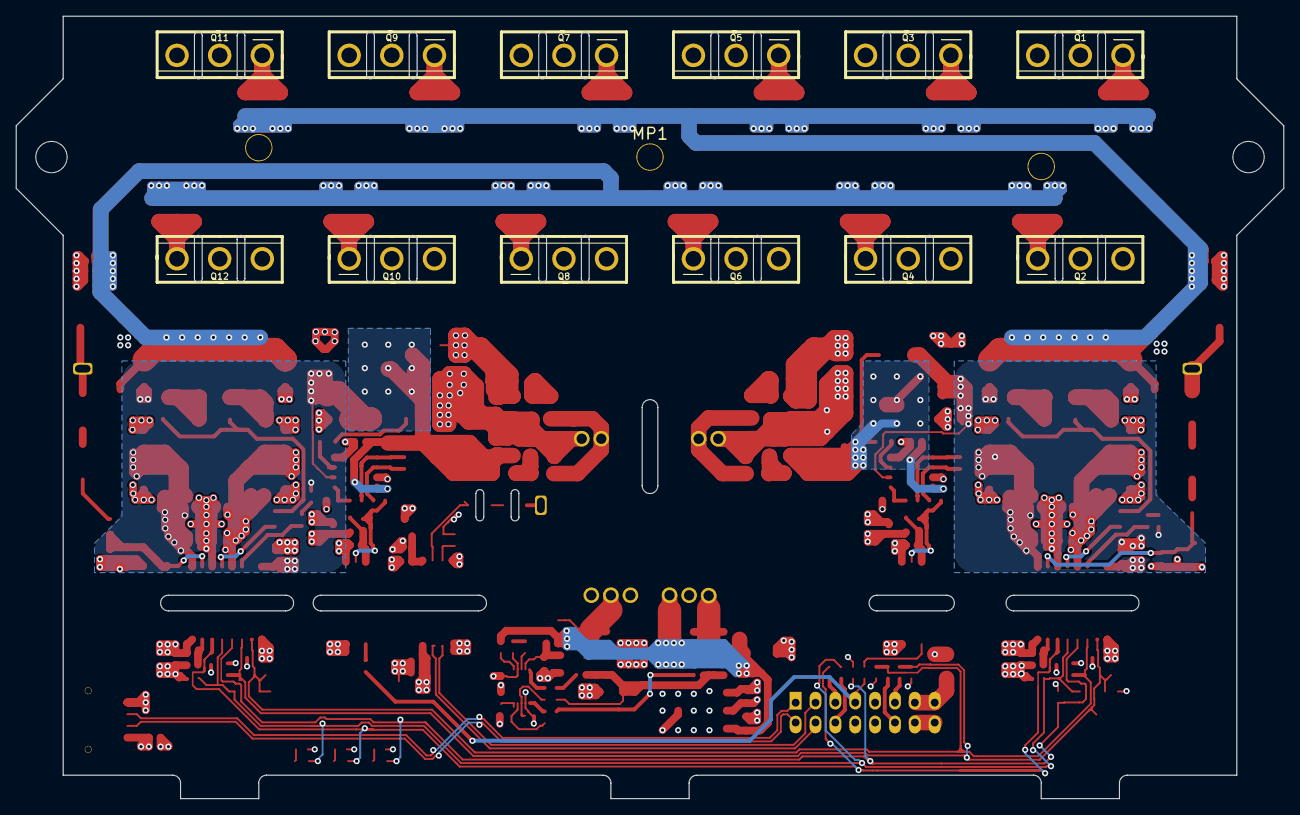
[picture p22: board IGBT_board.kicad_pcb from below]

Board: 4 copper layers, 162.0 x 100.0 mm, 259 parts (20 on the bottom side), 107 nets.

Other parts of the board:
eREF**: MountingHole_6mm; MountingHole_4mm

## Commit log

2016-11-04 Added schematic of power transistors and caps, basic layout and watercooling
    [EPCOS_film_cap.fcstd, EPCOS_film_cap_B32796G3166.step, IGBT_board.kicad_pcb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]
2016-11-06 Draft of bus bars and mounting points
    [IGBT_board.kicad_pcb, IGBT_board.sch, inverter.fcstd]
2016-11-09 Added IGBT gate driver circuit and isolated power supply
    [IGBT_board.kicad_pcb, IGBT_board.sch, IGBT_driver.sch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]
2016-11-12 Add footprints, more layout and graphics
    [IGBT_board.kicad_pcb, IGBT_board.sch, IGBT_driver.sch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]
2016-11-20 Add IGBT driver datasheet
2016-11-20 Larger gate resistors, added gate caps, added comments and images to the schematic
    [IGBT_board.kicad_pcb, IGBT_board.sch, IGBT_driver.sch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]
2016-11-21 Added schottky between gate and 15v supply
    [IGBT_driver.sch]
2016-11-22 Updated 3D assembly. Copper cutouts, current transducer, updated pcb
    [half bridge.fcstd, inverter.fcstd]
2016-11-23 Added 3D models, connector, more layout, updated readme
    [BAS-M-R0002.step, HASS_XXX-P.step, HASS_XXX-P.stp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]
2016-11-23 Added testpoints
    [IGBT_board.kicad_pcb, IGBT_board.sch, IGBT_driver.sch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]
2016-11-24 Change gate diode direction, I thought Ron should be smaller than Roff, and its not
    [IGBT_driver.sch]
2016-11-24 Added NAND gates for shoot-through protection, and to configure the driver so when a fault is asserted the whole inverter will be shut down until a reset signal is issued
    [IGBT_board.sch, IGBT_driver.sch, IGBT_driver_power_suply.sch]
2016-11-26 Updated viable IGBT part#, selected infineon IGBT as project default
    [IGBT_board.sch, IGBT_driver.sch]
2016-11-26 Changed GND copper plane to avoid coupling between phase output and controller GND (112pF->13pF)
    [IGBT_board.kicad_pcb]
2016-11-26 Added on board 3.3v regulator, power supply fuse and some resistors to protect digital lines
    [IGBT_board.sch]
2016-11-26 Added board dimensions and improved gate return path
    [IGBT_board.kicad_pcb]
2016-11-27 Update 3D assembly with smaller phase copper sheet
    [half bridge.fcstd]
2016-11-27 Sync layout with schematic
    [IGBT_board.kicad_pcb]
2016-11-27 Fixed schematic label and more layout
    [IGBT_board.kicad_pcb, IGBT_board.sch, IGBT_driver.sch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]
2016-12-18 Added gate voltage control, more decoupling pads for the buffer transistors, added notes
    [IGBT_board.sch, IGBT_driver.sch, IGBT_driver_power_suply.sch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]
2016-12-20 Better layout. Added 3d models and updated cache lib
    [IGBT_board.kicad_pcb, soic_6_75x46_p127.FCStd, soic_6_75x46_p127.step]
2016-12-20 Removed old comments, added notes, connected programmable -VEE
    [IGBT_board.sch, IGBT_driver.sch, IGBT_driver_power_suply.sch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]
2016-12-21 Updated copper planes. Added vias
    [IGBT_board.kicad_pcb]
2016-12-21 Improved gate traces using 4 layers. Increased TO-247 creepage with slots
    [IGBT_board.kicad_pcb]
2016-12-21 Added phase voltage sensing
    [IGBT_board.sch, IGBT_driver.sch, IGBT_driver_power_suply.sch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]
2016-12-21 Connected phase sensing, added images
    [IGBT_board.sch, phase_voltage_sensor.sch]
2016-12-22 Phase voltage sensing laid out
    [IGBT_board.kicad_pcb, IGBT_board.sch, IGBT_driver.sch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]
2016-12-24 Added mounting points, trying 12 pos connector. Added 3d models
    [IGBT_board.kicad_pcb, M3_SMD_Standoff.fcstd, M3_SMD_Standoff.step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]
2016-12-26 Updated gate resistor rating, qty and part#, updated desat blocking diode with much beetter recovery time
    [IGBT_board.sch, IGBT_driver.sch, IGBT_driver_power_suply.sch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]
2016-12-26 Added comments before I forget things, changed X5R to X7R. Updated PCB
    [IGBT_board.kicad_pcb, IGBT_board.sch, IGBT_driver.sch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]
2016-12-27 Power supply sync input. And more comments
    [IGBT_board.sch, IGBT_driver.sch, IGBT_driver_power_suply.sch]
2016-12-30 Changed power supply from 15/-8V to +15/-15V se we can make better use uf programmable -VEE. Changed connector to 14pos. Connected some missing signals. Updated layout
    [IGBT_board.kicad_pcb, IGBT_board.sch, IGBT_driver.sch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]
2016-12-31 Changed isolated amplifier from AMC1200 to AMC1301 because it has reinforced isolation. This required a different layout
    [61001421121-rev1.step, 61031221121-rev1.stp, IGBT_board.kicad_pcb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]
2017-01-10 More .step 3D models included for better portability
    [IGBT_board.kicad_pcb, c_0603_h078.step, c_0805_h078.step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]
2017-01-10 For some reasong eyrie needs the schematics and cache file synced
    [IGBT_board.sch, IGBT_driver.sch]
2017-01-11 Larger 2512 gate resistors
    [750342312.fcstd, IGBT_board.kicad_pcb, IGBT_board.sch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]
2017-01-17 Added CERN Open Hardware Licence ("CERN OHL") version 1.2 documents
    [IGBT_board.sch, IGBT_driver.sch, IGBT_driver_power_suply.sch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]
2017-02-10 Addded schematic image
2017-07-17 Added current sensor connector. Layout is now symmetrical
    [EPCOS_film_cap.fcstd, EPCOS_film_cap_B32796G3166.step, HTFS_XXX-P.stp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]
2018-11-12 Add gate driver load to enable 2 step turnoff in buffered configuration. Updated layout.
    [IGBT_board.kicad_pcb, IGBT_board.sch, IGBT_driver.sch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]

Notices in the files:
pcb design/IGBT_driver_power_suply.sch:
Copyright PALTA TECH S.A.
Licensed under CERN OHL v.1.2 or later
